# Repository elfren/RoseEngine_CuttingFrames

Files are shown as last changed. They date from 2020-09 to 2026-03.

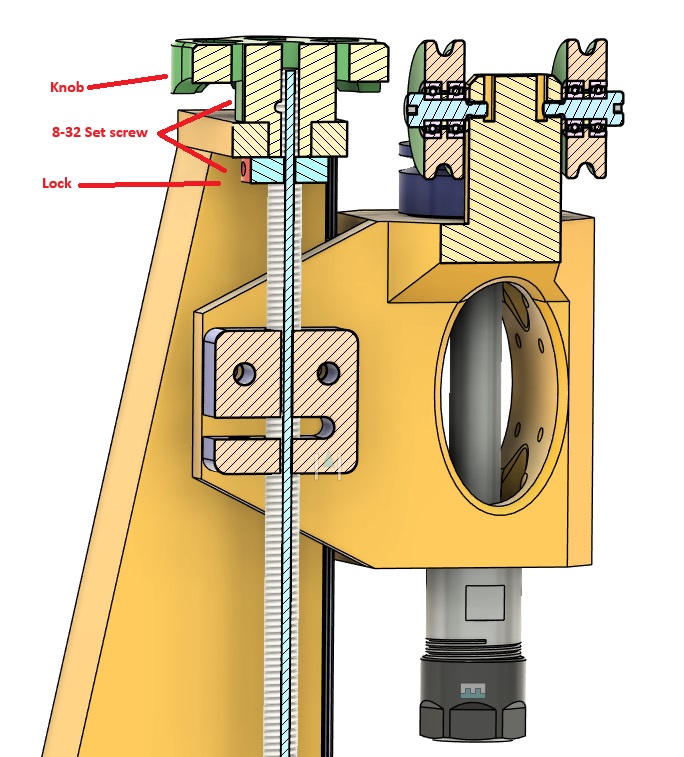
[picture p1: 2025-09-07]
3d_Printed_Frames/VerticalDrillingFrame/LeadscrewAssembly.jpg

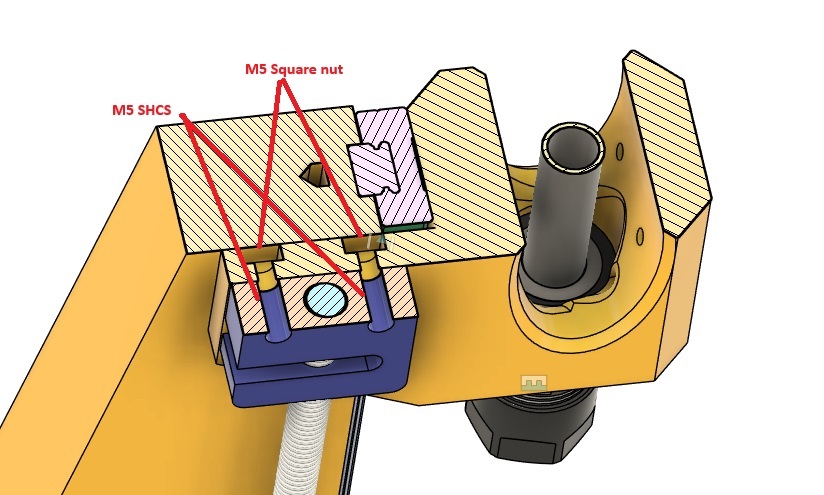
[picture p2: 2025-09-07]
3d_Printed_Frames/VerticalDrillingFrame/LeadscrewNut.jpg

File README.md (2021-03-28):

Fusion 360 models for rose engine cutting frames with adjustable pulley for belt length.

Two models are provided.  
    Sliding: The overhead drive pulley is attached to a slider which moves up and down to adjust belt tension.
    Slotted: The overhead drive pulley slides up and down in a slot.
Part numbers are McMaster-Carr numbers.

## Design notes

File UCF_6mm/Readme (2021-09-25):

UCF which takes 6mm or smaller cutters.

 Toolpaths for the tower are included.  Machining the other parts will probably be on manual machines. 
 The bearing holes should be bored with the arms attached.  
 The holes for the split pins should be drilled after the bearing holes and while the cutter mount arms are still attached to the main arm.

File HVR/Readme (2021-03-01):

Combined horizontal, vertical, and right angle cutting frame.

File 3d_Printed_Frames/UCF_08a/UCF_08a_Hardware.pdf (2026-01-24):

### Main Body Hardware

Qty Description
4 M695ZZ bearing
1 M5x20 shoulder bolt M4x0.7 thread 2 M5x10 shoulder bolt M4x0.7 thread 1 M5x30 shoulder bolt M4x0.7 thread 4 M4x7x7x3 square nut
1 M4x12x12x1 square washer
1 16x150x1.5 Stainless tube
1 M5x12x12x1 square washer 1 5x0.2 bearing shim
6 M3x5.5x2.25 square nut
6 M3x6 set screw
1 Bearing spacer 5mm X 8mm X 5.5mm (Brass tube or printed) 1 2mm X 310mm round poly belt
1 3mm round poly belt (Length depends on overhead drive)

### Insert Cutter Head Hardware

1 TDHB07T1202 Triangular Insert
1 M2.2x6 Torx insert screw
1 Bearing spacer 5mm X 8mm X 6mm (Brass tube or printed) 2 M695ZZ bearing
1 Brass flat stock 4.5mm X 6.5mm X 3mm

### Round Cutter Head Hardware

1 Engraving bit 0.125"
2 M3x6mm set screw
1 Bearing spacer 5mm X 8mm X 6mm (Brass tube or printed) 2 M695ZZ bearing
3 M5x6mm set screw

### Main Body 3D Print (ABS-GF)

1 UCF_08_MainBody + Supports
2 Idler Pulley
1 Double Pulley
1 Bearing spacer 5mm X 8mm X 5.5mm (Brass tube or printed) 1 Knob

### Insert Cutter Head 3D Print (ABS)

1 Cutter Head
1 Bearing spacer 5mm X 8mm X 6mm (Brass tube or printed) 1 Insert Top Lock. This is optional for insert cutter heads.

### Round Cutter Head 3D Print (ABS)

1 Cutter Head
1 Bearing spacer 5mm X 8mm X 6mm (Brass tube or printed) 1 Sharpening jig 60 degrees
1 Sharpening jig 90 degrees
1 Sharpening jig 120 degrees

### Tools

Metric Allen wrench set
M3 Tap (Round engraving bit cutter head) M2.2 Tap (Insert nut cutter head)
1.75mm drill or #51 (0.067") for M2.2 thread .125" drill (Round engraving bit cutter head)

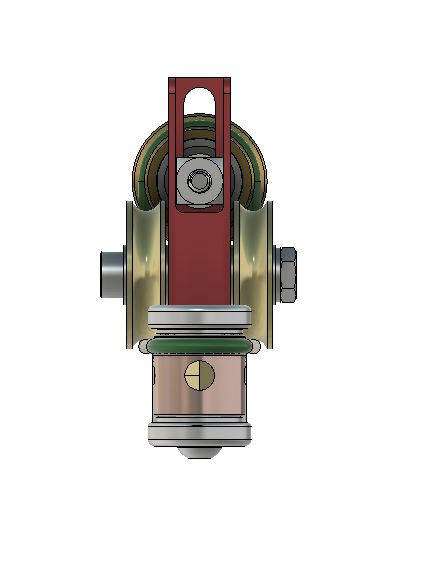
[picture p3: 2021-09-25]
UCF_6mm/Images/UCF_6mm_U_Front.JPG

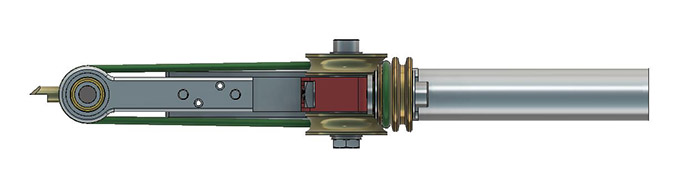
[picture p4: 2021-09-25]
UCF_6mm/Images/UCF_6mm_U_Top.JPG

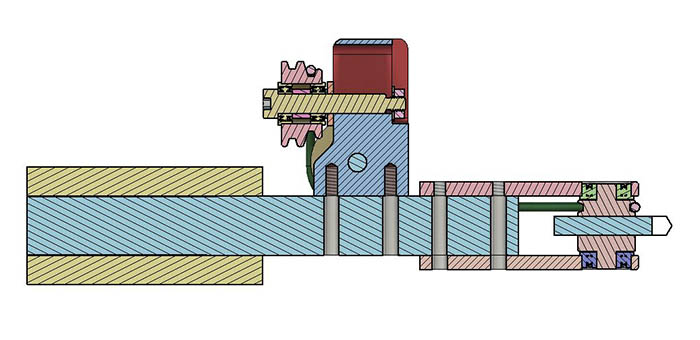
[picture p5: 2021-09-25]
UCF_6mm/Images/SectionView.JPG

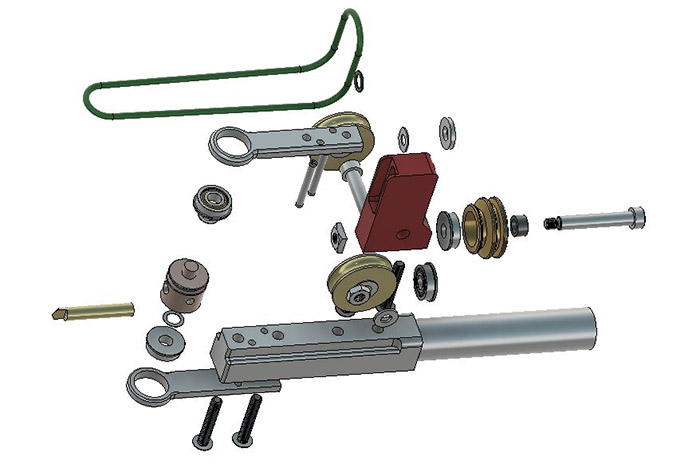
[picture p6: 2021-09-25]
UCF_6mm/Images/UCF_6mm_U_Explode.JPG

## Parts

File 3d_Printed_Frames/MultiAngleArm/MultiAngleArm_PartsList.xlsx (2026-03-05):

Part Name | Quantity | Material | Fasteners
Multi_Angle_Arm | 1 | ABS-GF | M3 Square Nut | 3
Modifier_TF | 1 | ABS-GF | M4 Square Nut | 2
Shaft 0.75"x4" | 1 | Steel | M5 Square Nut | 5
MGN12x100mm Rail | 1 | Steel | M3x6 Set Screw | 4
MGN12C Carriage | 2 | Steel | M5x6 Set Screw | 3
IdlerAdjuster | 1 | ABS-GF | M3x8 SHCS | 4
Leadscrew T8x150mm | 1 | Steel | M3x10 SHCS | 6
TR8x2 AntiBacklash Nut | 1 | Steel | M4x10 SHCS | 2
Leadscrew Lock | 1 | ABS,Brass, or Steel | M5x12 SHCS | 2
HTD-3-60t | 1 | ABS-GF | M4x10 Shoulder Bolt (M3x6mm thread) | 2
Stepper_NEMA17 | 1 | Steel
GT2-3-15t or HTD-3-15t | 1 | Aluminum or ABS-GF
GT2-3 or HTD-3 Timing Belt 80T, 240L,6mm | 1 | Steel
Drilling Frame
DrillFrame_Housing | 1 | ABS-GF | M4 Square Nut | 2
IdlerPulley M695_ZZ | 2 | ABS-GF | M3x6 Set Screw | 2
Spacer_Idler 5x7.5x1.5 | 1 | ABS,Brass, or Steel | M3x8 SHCS | 8
M695 bearing | 2 | Steel | M5x10 Shoulder Bolt | 2
C12-ER16-L100 | 1 | Steel
MR6201_ZZ Bearing | 2 | Steel
Pulley_12mm_Bore | 1 | ABS-GF
C20-ER25-L100 or C20-ER16-100L | 1 | Steel
MF6804_ZZ Bearing | 2 | Steel
Pulley_20mm_Bore | 1 | ABS-GF
UCF
UCF_Base_05c | 1 | ABS-GF | M4_Nut | 2
UCF_Top | 1 | ABS-GF | M4 Square Nut | 2
Idler_Pulley_M695_ZZ | 4 | ABS-GF | M4_Washer | 2
M695_ZZ Bearing | 6 | Steel | M5x6 Set Screw | 8
DoublePulley | 1 | ABS-GF | M5x25 Shoulder Bolt | 3
Spacer_DoublePulley 5x7x4.3 | 1 | ABS,Brass, or Steel | M5x20 Shoulder Bolt | 1
Shaft_10x100 | 1 | Steel
BearingShim_5x7 | 2 | Steel
Round Poly Belt 2x300 | 1 | Polypropylene
Cutter Heads
CutterHead_TDHB071202_CW_Nut | 1 | ABS | M2.2x0.45 Torx Head Screw | 1
Spacer_5x7x6.1 | 1 | ABS,Brass, or Steel
M695_ZZ Bearing | 2 | Steel
TDHB07T1202 | 1 | Carbide
Insert_Top_Lock | 1 | ABS
InsertNut_CW | 1 | Brass
CutterHead_TDHB071202_CCW_Nut | 1 | ABS | M2.2x0.45 Torx Head Screw | 1
Spacer_5x7x6.1 | 1 | ABS,Brass, or Steel
M695_ZZ Bearing | 2 | Steel
TDHB07T1202 | 1 | Carbide
Insert_Top_Lock | 1 | ABS
InsertNut_CCW | 1 | Brass
CutterHead_TDHB071202_CW | 1 | ABS | M2.2x0.45 Torx Head Screw | 1
Spacer_5x7x6.1 | 1 | ABS,Brass, or Steel
M695_ZZ Bearing | 2 | Steel
TDHB07T1202 | 1 | Carbide
Insert_Top_Lock | 1 | ABS
CutterHead_TDHB071202_CCW | 1 | ABS | M2.2x0.45 Torx Head Screw | 1
Spacer_5x7x6.1 | 1 | ABS,Brass, or Steel
M695_ZZ Bearing | 2 | Steel
TDHB07T1202 | 1 | Carbide
Insert_Top_Lock | 1 | ABS
CutterHead_Round | 1 | ABS | M3x6 Set Screw | 2
Spacer_5x7x6.1 | 1 | ABS,Brass, or Steel | M5x6 Set Screw | 3
M695_ZZ Bearing | 2 | Steel
0.125" diameter cutter | 1 | Carbide
Sharpening Jig 60 degree | 1 | ABS
Sharpening Jig 90 degree | 1 | ABS
Sharpening Jig 120 degree | 1 | ABS

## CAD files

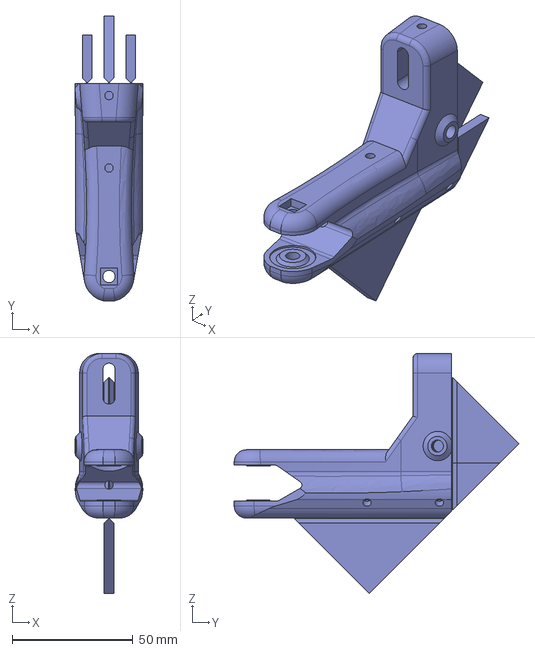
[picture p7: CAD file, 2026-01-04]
3d_Printed_Frames/UCF_08a/MainBody/UCF_08_MainBody/MainBody_3D_UCF_Insert_08_WithSupports.step
28.2 x 117.9 x 99.5 mm

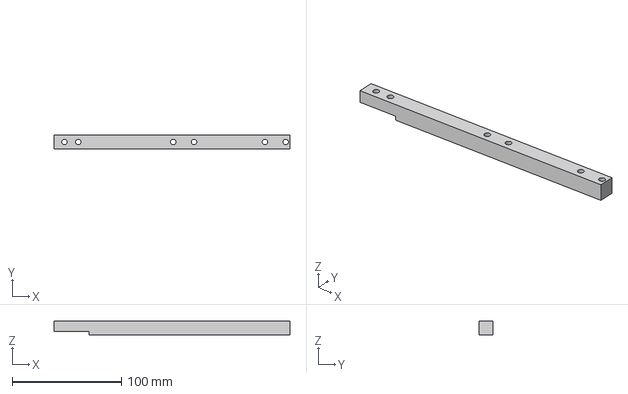
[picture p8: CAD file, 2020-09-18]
Horizontal/Models/Step/MainArm_Square.step
215.9 x 12.7 x 12.7 mm

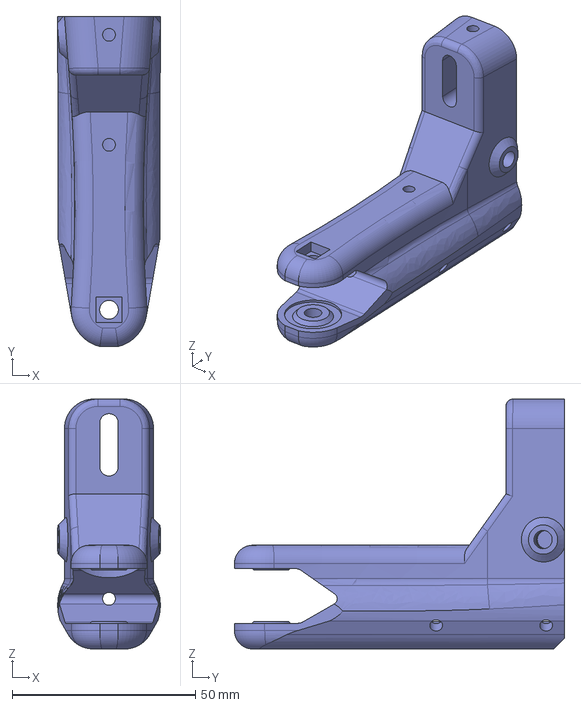
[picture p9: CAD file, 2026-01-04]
3d_Printed_Frames/UCF_08a/MainBody/UCF_08_MainBody/MainBody_3D_UCF_Insert_08.step
28.2 x 90.1 x 68.2 mm

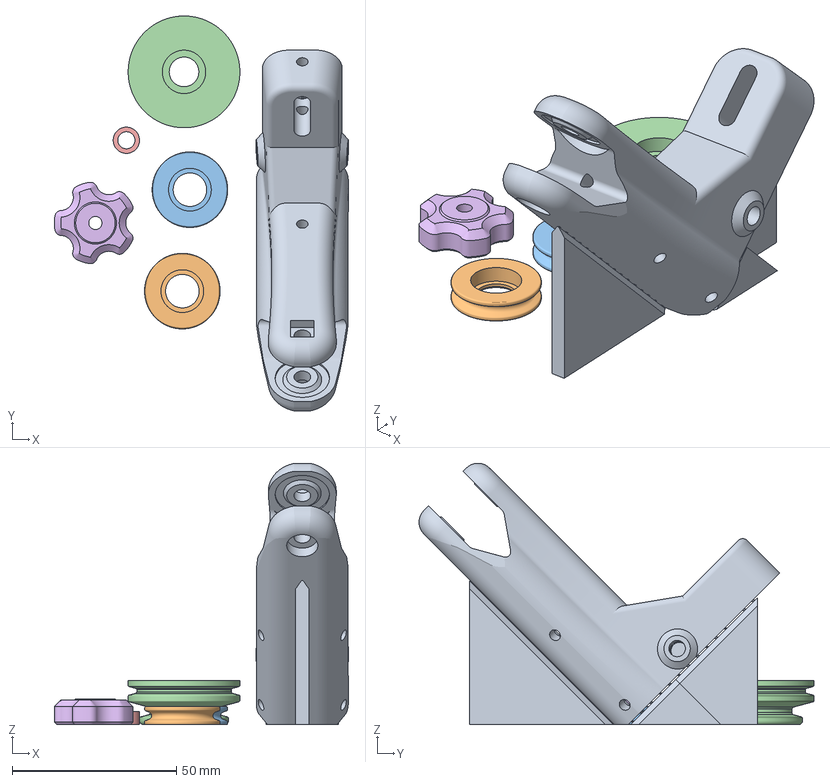
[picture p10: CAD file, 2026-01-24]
3d_Printed_Frames/UCF_08a/UCF_08a_Main.3mf
89.6 x 120.2 x 79.6 mm
MainBody_3D_UCF_Insert_08_WithSupports.step
Idler_5mm.step x 2
DoublePulley_08_UCF.step
Spacer_DoublePulley_08UCF.step
Knob_03.step

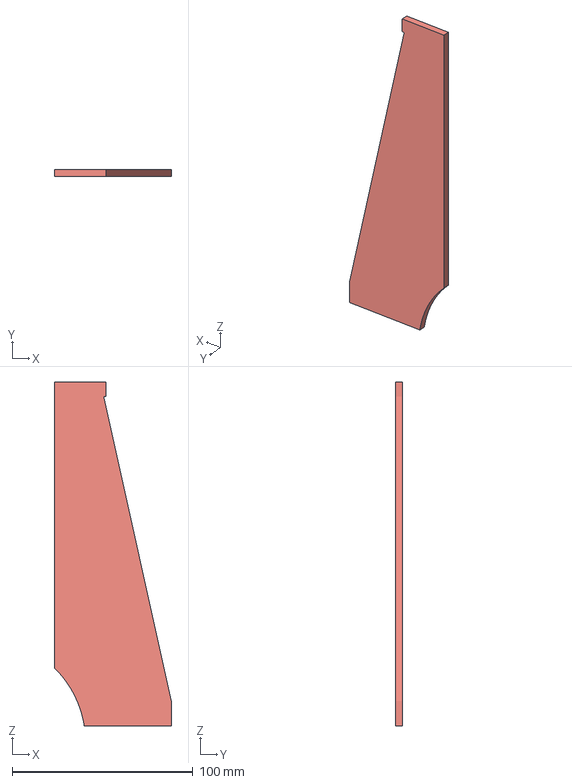
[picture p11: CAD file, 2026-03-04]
3d_Printed_Frames/MultiAngleArm/3DPrint_Slicer_Files/MAA_Modifier_MainArm.3mf
64.8 x 4.00 x 190.1 mm

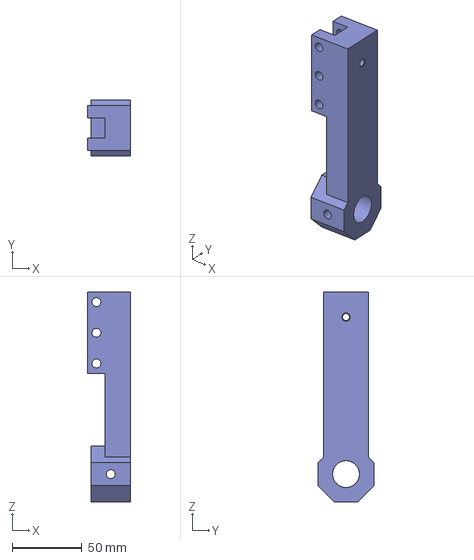
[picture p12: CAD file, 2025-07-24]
3d_Printed_Frames/Angle/MainArm_04.step
30.5 x 40.0 x 150.6 mm

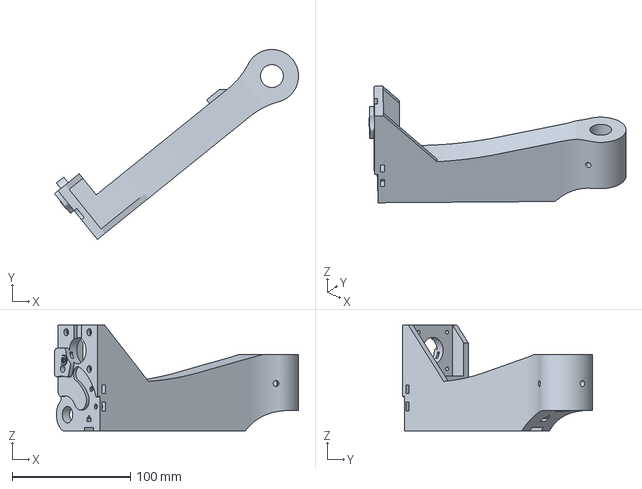
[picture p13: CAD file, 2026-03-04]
3d_Printed_Frames/MultiAngleArm/3DPrint_Slicer_Files/MAA_MainArm.3mf
206.6 x 160.8 x 89.4 mm

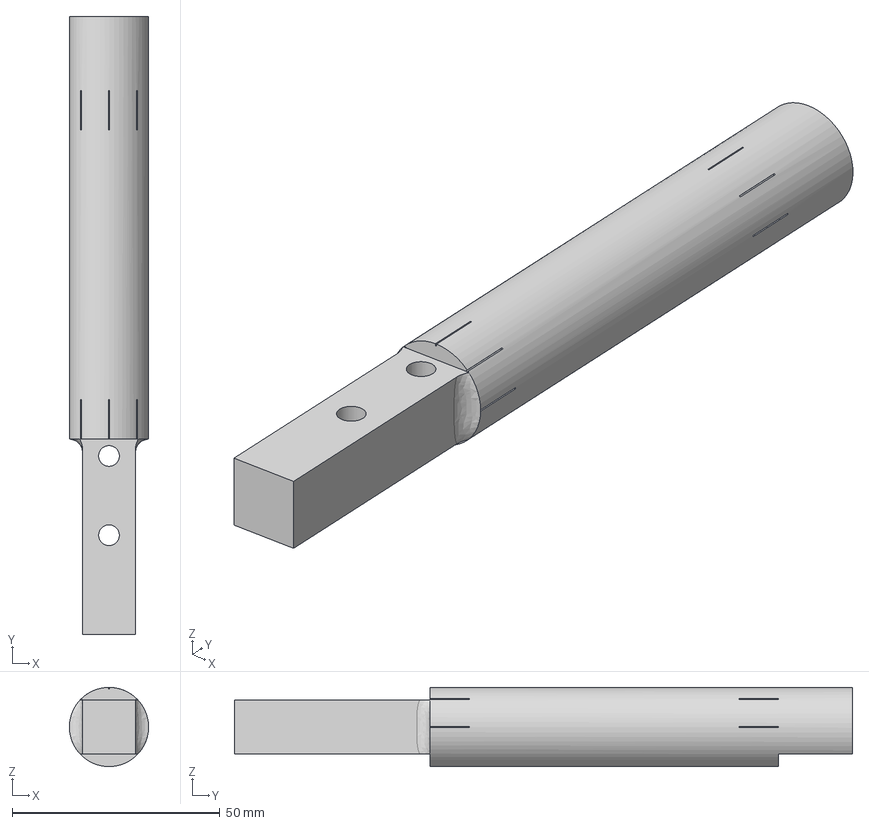
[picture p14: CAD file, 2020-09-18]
UCF-Slotted/Models/Step/UCF_MainArm.step
19.0 x 148.6 x 19.0 mm

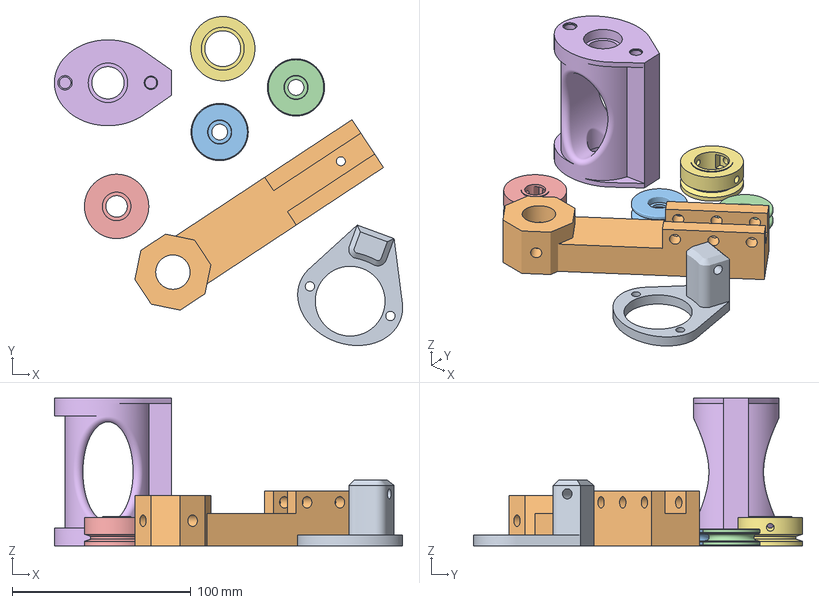
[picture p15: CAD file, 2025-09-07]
3d_Printed_Frames/Angle/AngleDrillFrame_12_and_20mm_Bore.3mf
194.8 x 184.0 x 82.5 mm
PulleyStand_04.step
MainArm_04.step
IdlerPulley_03.step x 2
Pulley_12mm_Bore.step
Housing_22mm_OD.step
Pulley_20mm_Bore.step

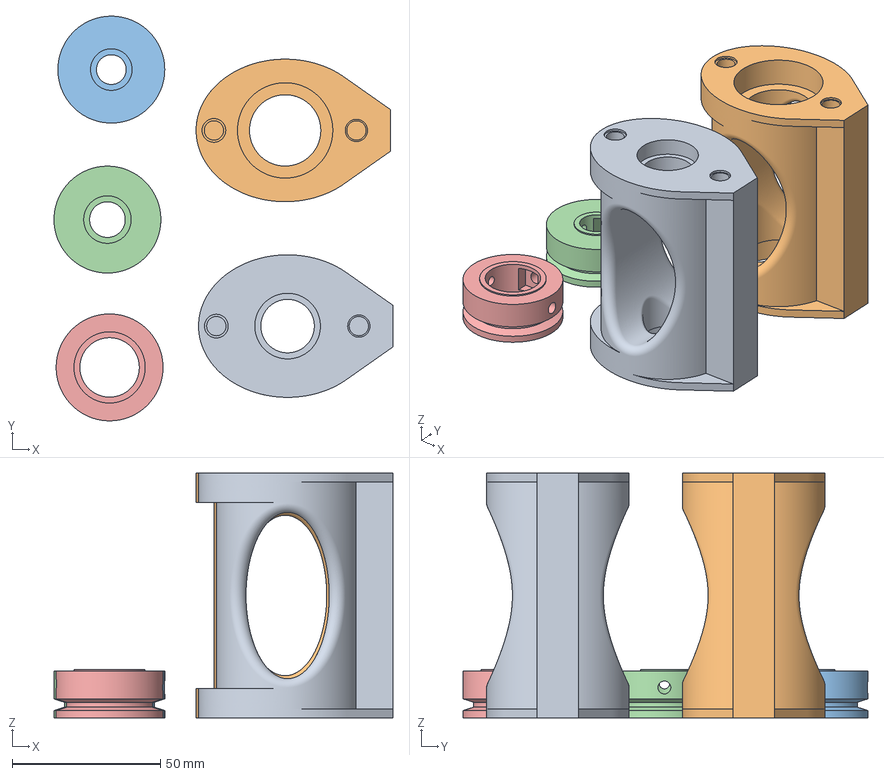
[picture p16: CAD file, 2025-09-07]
3d_Printed_Frames/Drilling_Frame/3D_DrillFrame.3mf
114.2 x 136.3 x 82.5 mm
Housing_22mm_OD.step
Housing_32_OD.step
Pulley_10mm_Bore.step
Pulley_12mm_Bore.step
Pulley_20mm_Bore.step

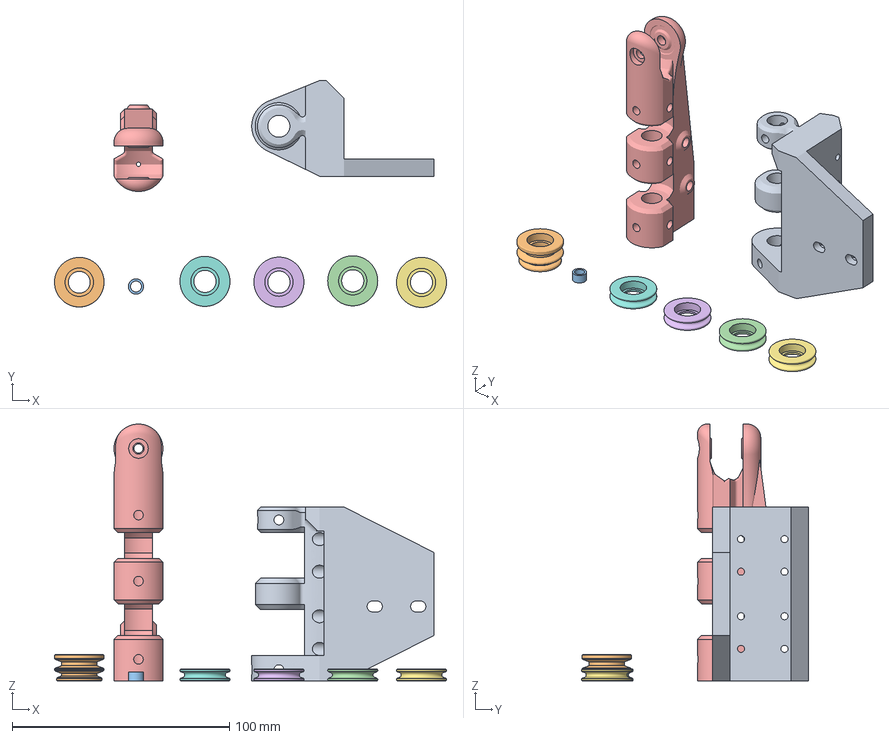
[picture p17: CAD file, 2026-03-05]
3d_Printed_Frames/MultiAngleArm/3DPrint_Slicer_Files/MAA_UCF .3mf
180.3 x 104.3 x 118.2 mm
Base_05c .step
DoublePulley_08.step
DoublePulley_Spacer.step
Idler_5mm.step x 4
MAA_UCF.step

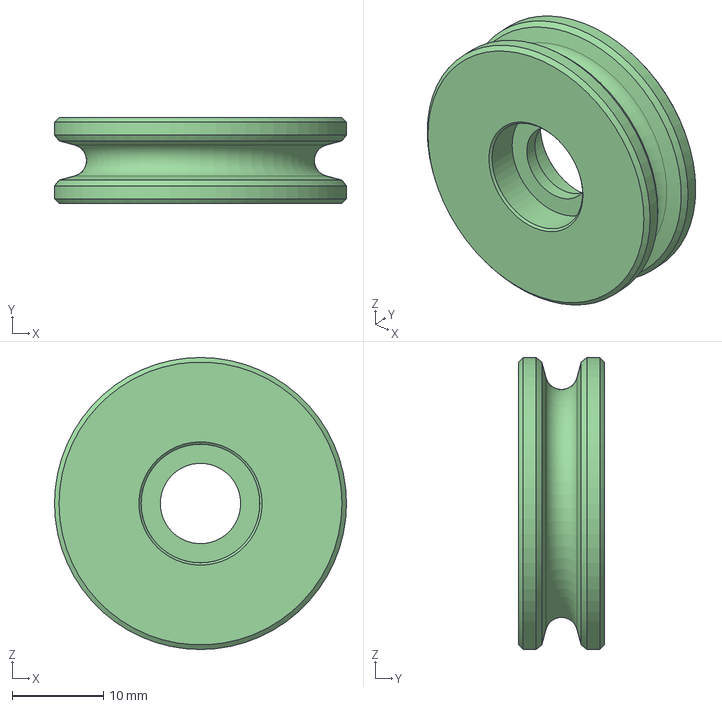
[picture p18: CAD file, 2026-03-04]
3d_Printed_Frames/MultiAngleArm/Drill_Frame/IdlerPulley_03.step
32.0 x 9.40 x 32.0 mm

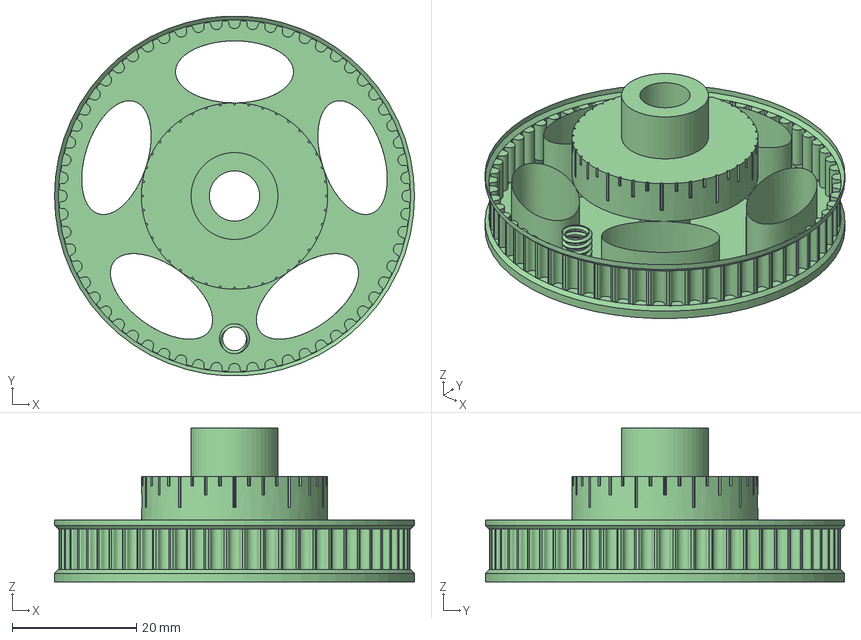
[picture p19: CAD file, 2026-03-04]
3d_Printed_Frames/MultiAngleArm/Main_Arm/Pulley_HTD-3-60t.step
58.0 x 57.9 x 24.8 mm

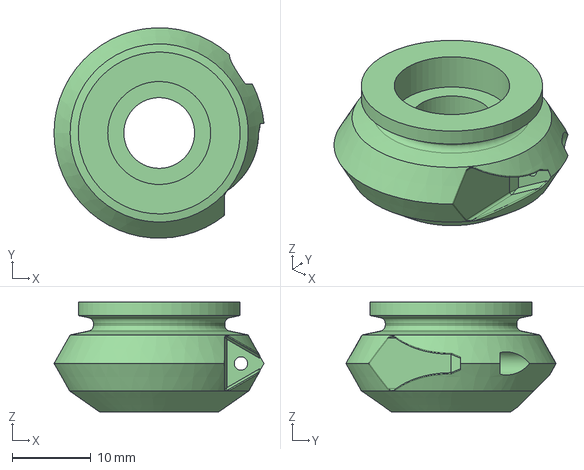
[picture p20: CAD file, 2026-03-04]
3d_Printed_Frames/MultiAngleArm/UCF/Insert_CutterHead/Plain/CutterHead_TDHB071202_CW.step
26.7 x 26.8 x 14.0 mm

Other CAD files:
3d_Printed_Frames/MultiAngleArm/UCF/MAA_UCF.step
3d_Printed_Frames/MultiAngleArm/UCF/Round_CutterHead/Cutterhead_Round_10b.step
3d_Printed_Frames/MultiAngleArm/UCF/Round_CutterHead/SharpeningJigs/Jig_60.step
3d_Printed_Frames/UCF_08a/CutterHeads_HexNuts/CutterHead_TPGH080201_CCW.gcode.3mf
3d_Printed_Frames/Angle/AngleDrillFrame_10mm_Bore.3mf
3d_Printed_Frames/Angle/IdlerPulley v7.step
3d_Printed_Frames/Angle/IdlerPulley_03.step
3d_Printed_Frames/Angle/InfillModifier_04.3mf
3d_Printed_Frames/Angle/PulleyStand_04.step
3d_Printed_Frames/Archive/3D_UCF.3mf
3d_Printed_Frames/Archive/3D_UCF.f3z
3d_Printed_Frames/Archive/3D_UCF_B_CutterHead_104zz.step
3d_Printed_Frames/Archive/3D_UCF_B_DoublePulley.step
3d_Printed_Frames/Archive/3D_UCF_B_Idler.step
3d_Printed_Frames/Archive/3D_UCF_Cutterheads.3mf
3d_Printed_Frames/Archive/CutterJig_120Degrees.step
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

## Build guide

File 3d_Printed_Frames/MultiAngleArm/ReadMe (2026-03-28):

Step files for each part are located in their individual folders. .3mf files are located in the folder, 3DPrint_Slicer_Files, as well as the individual folders.

Cutter heads are shared with UCF_08a.

Multi Angle Main Arm print files and filament type:
  MAA_MainArm.3mf (ABS-GF)
  MAA_Modifier_MainArm.3mf (Loaded as modifier in MAA_MainArm.3mf. 100% infill)
  MAA_Pulleys.3mf (ABS)
  
Drilling Frame:
  DrillFrame.3mf (ABS-GF)

UCF:
  MAA_UCF.3mf (ABS-GF)
  CutterHeads_Nuts.3mf (ABS)
  CutterHead_Round.3mf (ABS)

Notes:
Main arm should be printed on a raft to reduce warping.

Cutter heads should be printed with a 0.08mm layer height.  The others may be printed with a 0.2mm layer height (0.08mm layer height is OK, but will take much longer to print).
Insert cutter heads have CW and CCW versions. The round cutter head uses 0.125" engraving bits and can be configured for either CW or CCW.

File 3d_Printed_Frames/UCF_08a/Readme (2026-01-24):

Full assembly instructions are located in '3D Printed Universal Cutting Frame 8a.pdf'.
.3mf files include print profiles.
Step files are included in order to make modifications easier.

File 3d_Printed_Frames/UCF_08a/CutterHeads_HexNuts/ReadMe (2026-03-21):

These cutter heads use TDHB07T1202-PCD and TPGH080201-PCD diamond inserts. Each have CW and CCW versions.

The TPGH insert has an 11 degree top rake. The TDHB does not have a top rake.

The TDHB uses an M2.2x0.45 or a #2-56 torx head insert screw. A #2-56 nut is used. When using the M2.2 screw, tapping the nut with an M2.2 tap will ensure the threads won't bind.
 
The TPGH uses M2.5x0.45 torx head insert screw and M2.5 nuts. 

The TopLock is secured with ABS slurry (Acetone and ABS).  It provides more support for the insert.

Print these with ABS. Gcode files are sliced for a Bambu X1C with a 0.4mm nozzle. Layer height is .08mm.

The image shows the TPGH cutter head with supports for printing.

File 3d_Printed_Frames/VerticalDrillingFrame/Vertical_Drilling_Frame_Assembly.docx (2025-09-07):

# Vertical Drilling Frame Assembly

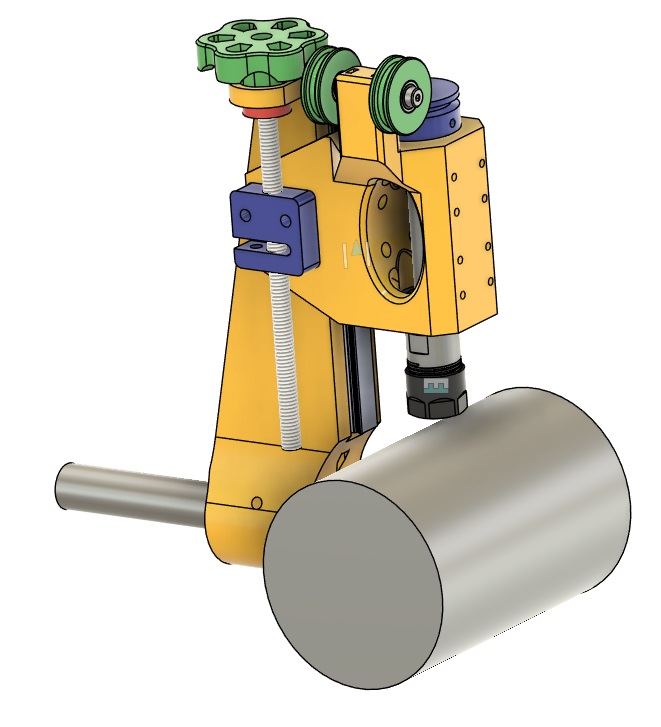
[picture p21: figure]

# Parts List:

ER Chuck Housing
QTY | Hardware
1 | MGN12 rail. 150mm long
2 | MGNC carriage
4 | M3x8mm SHCS
2 | M3x12mm SHCS
1 | C12-ER16-100L
2 | M5x10mm Shoulder Bolt with M4 threads (6mm long)
2 | M5x0.2 Bearing Shim
2 | M5 Washer 1mm thick
2 | M4 Square Nut
2 | 8-32x0.1875" Set Screw
2 | M5 Square Nut
2 | MR6201_ZZ Bearing
4 | MR695_ZZ Bearing
Main Arm
3 | M5x5mm Set Screw
3 | M5 Square Nut
1 | 0.75"x5" Steel Shaft
1 | 250-104 Boring Bar Tool Holder
2 | M3 Square Nut

Leadscrew
1 | TR8 Leadscrew 2mm pitch, 2mm lead
1 | Anti-Backlash Nut to fit
2 | M5x20 SHCS
5 | 8-32x0.1875" Set Screw
| 3D printed parts
1 | ER Chuck Housing
2 | Idler Pulley
2 | Idler Spacer (5x7x1.5mm)
1 | Drive Pulley
1 | Leadscrew Knob
1 | Leadscrew Lock
1 | Main Arm

# Main Arm:

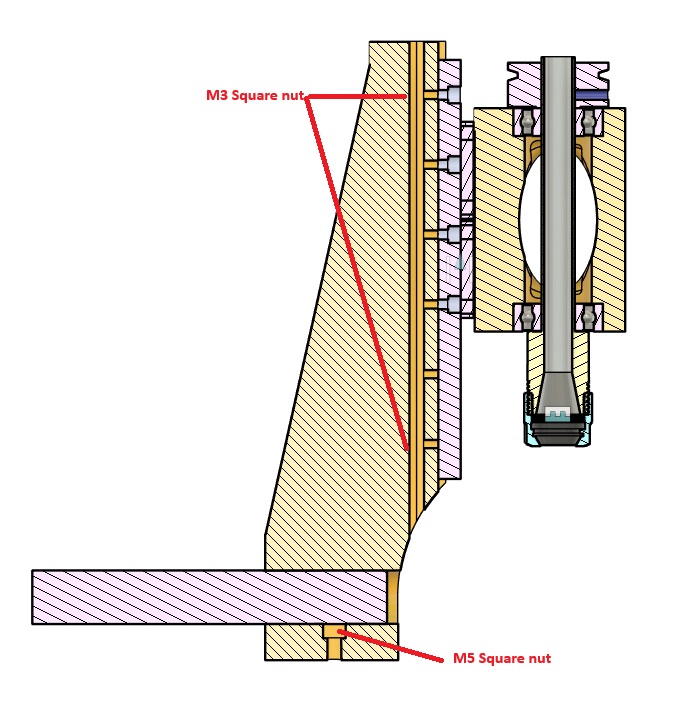
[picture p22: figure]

M3 tap 6 of the 8 holes to attach linear slide to arm. Drill the two end holes with 1/8th inch or 3.5mm drill. Insert the two M3 square nuts. Note: M3 nuts can be used on all of the holes, but may be difficult to install.

Attach the ¾” shaft to the arm using the M5 square nuts and set screws. Note: M5 SHCS may be used instead of the set screws.

Attach the linear rail to the arm.

# Spindle Housing:

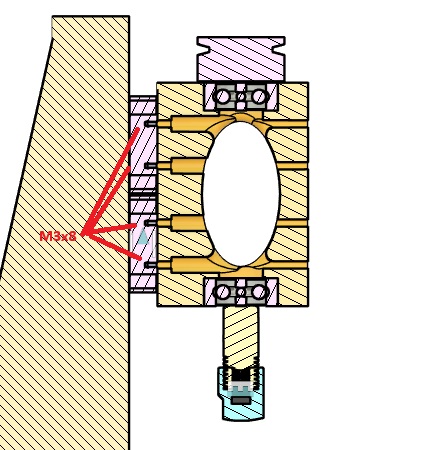
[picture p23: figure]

Press the MR6201_ZZ bearings into the housing.

Fasten the housing to the linear rail carriages using M3x8 SHCS.

Install the ER16 chuck.

Install the drive pulley using two 8-32 set screws.

# Idler Pulleys:

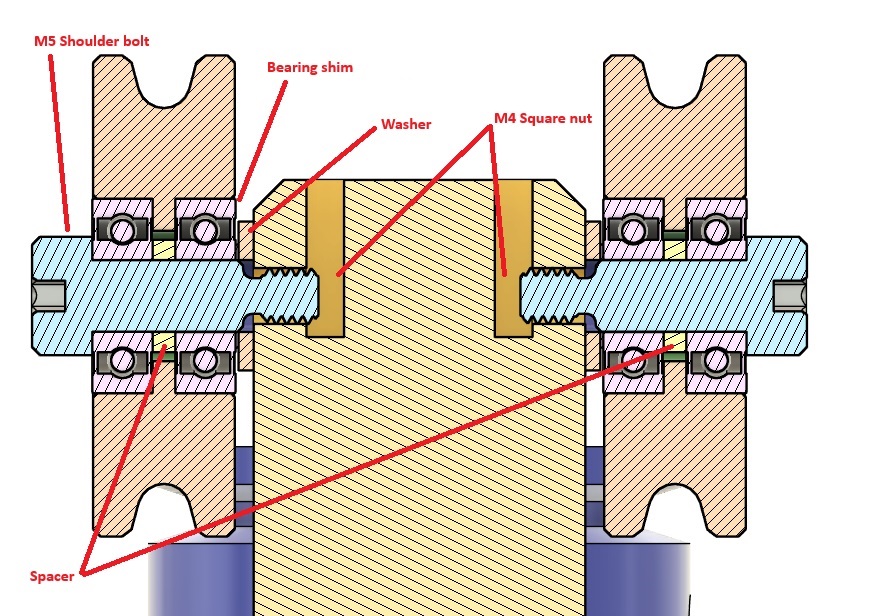
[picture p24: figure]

Press the M4 square nuts into the top of the housing.

Press the MR695_ZZ bearings into the idler pulleys making sure the spacer is installed. Insert the M5 shoulder bolt, add the bearing shim and the washer, then attach the idler pulley to the housing.

# Leadscrew


Install M5 square nuts in the housing. Attach the anti-backlash nut using M5 screws.


Tap the knob and the lock for 8-32 set screws.

Attach the knob, lock, and leadscrew.

# 3D Print

VerticalDrillFrame.3mf is optimized for a Bambu X1C printer.

Print Settings:

- 8 Walls
- 40% Infill, Cubic pattern
- Main Arm has a 100% infill modifier in the center
- Support: Tree Slim

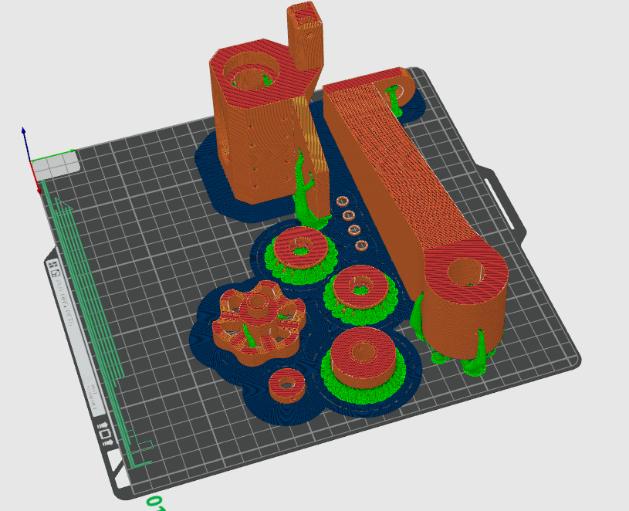
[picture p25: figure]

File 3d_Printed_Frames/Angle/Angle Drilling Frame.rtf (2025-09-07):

Angle Drilling Frame

This uses the 3d printed drilling frame in addition to a rotatable arm. It is held in an AXA boring bar holder.
Parts List:
Quantity | Description
4 | 695 Bearing (no flange) used in the idler wheels
2 | M5x10 Shoulder bolt with M4 thread
8 | M5 Heat set insert
2 | M4 Heat set insert
1 | 3/4"x4.125" Steel rod
6 | M5x12 SHCS
1 | AXA holder 250-104
1 | 3d printed drill frame with ER chuck
2 | 3d printed pulleys
1 | 3d printed main arm
1 | 3d printed pulley mount

3d Print Settings:
Setting | Value
Filament | ABS-GF
Walls | 8
Infill % | 40
Infill Pattern | Cubic
Support | Tree Slim
Brim | Outer 15mm

The file, AngleDrillFrame_10mm_Bore.3mf, contains all of the parts for the drill frame housing and the angle drill frame parts for an ER chuck with a 10mm shaft.
The file, AngleDrillFrame_12_and_20mm_Bore.3mf, contains all of the parts for the drill frame housing and the angle drill frame parts for an ER chuck with a 20mm and a 12mm shaft (Only the pulley differs).

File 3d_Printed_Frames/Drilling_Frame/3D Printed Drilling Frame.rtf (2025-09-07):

3D Printed Drilling Frame

There are two 3d printed parts, the main housing (green), and the drive pulley (yellow). The housing is designed to fit in an AXA tool holder. There are two versions of the main housing, one using 32mm OD bearings, and one using 22mm OD bearings. There are three versions of the pulley, one for each shank diameter; 20mm, 12mm, and 10mm. Any ER chuck with one of those shank diameters will work. The chuck must be at least 100mm long. 150mm chucks will also work. 20mm shanks will use F6804ZZ or 6804ZZ bearings. 12mm shanks will use F6201ZZ or 6201ZZ bearings. 10mm shanks will use F6900ZZ or 6900ZZ bearings.
The pulley is secured with two 8-32 x ¼” set screw in captured 8-32 square nut
Parts List

Quantity | Description
1 | 3d printed housing
1 | 3d printed Pulley
1 | ER Chuck
2 | 8-32 square nut
2 | 8-32 x 1/4" set screw
2 | Bearings

3d Print Settings:
Setting | Value
Filament | ABS-GF
Walls | 8
Infill % | 40
Infill Pattern | Cubic
Support | Tree Slim
Brim | Outer 15mm

The file, 3D_DrillFrame.3mf, contains all of the versions. Remove the unwanted ones before printing.

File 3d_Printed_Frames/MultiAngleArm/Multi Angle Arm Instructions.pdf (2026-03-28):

# Multi Angle Arm

## With

# Drilling Frame and Universal Cutting Frame

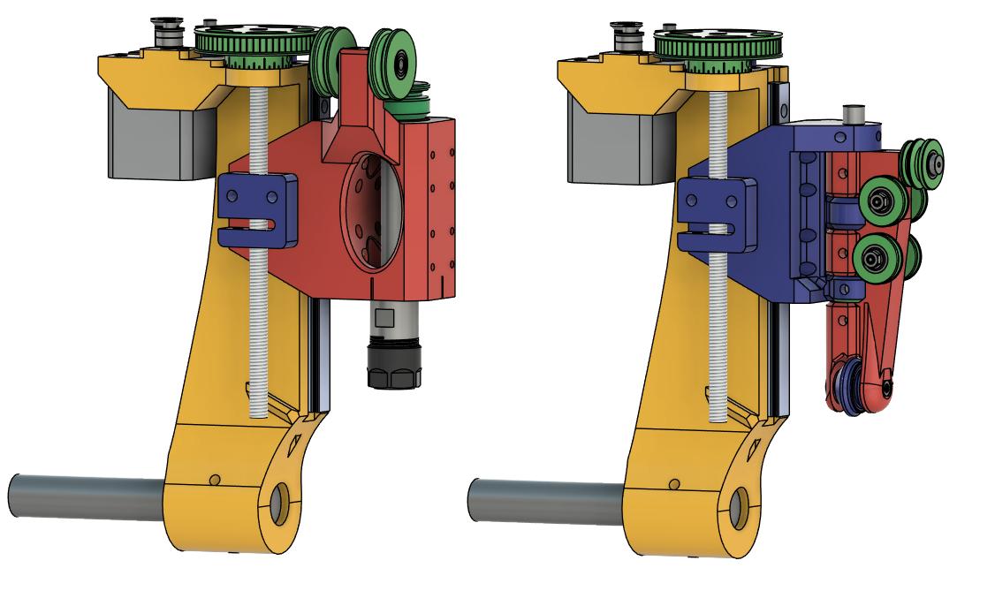
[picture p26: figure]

### The MultiAngleArm (MAA) is designed to hold a cutter above the workpiece at any angle between 90 and 180 degrees. The drilling frame rotates the tool parallel to the arm while

the universal cutting frame rotates the tool perpendicular to the arm and can be positioned

### at an angle to the arm. The stepper motor allows the depth of cut to be set

programmatically as well as moving the cutter in and out of the workpiece at the beginning and end of a cut. The MAA is attached to the toolpost with an AXA boring bar holder.

## Parts List

Part Name | Quantity | Material
Main Arm
Multi_Angle_Arm | 1 ABS-GF
Modifier_TF | 1 ABS-GF
Shaft 0.75"x4" | 1
MGN12x100mm Rail | 1

MGN12C Carriage | 2
IdlerAdjuster | 1 ABS-GF
F604ZZ Bearing | 2
M604ZZ Bearing | 2
Leadscrew T8x150mm | 1
TR8x2 AntiBacklash Nut | 1
Leadscrew Lock | 1 ABS,Brass, or Steel
HTD-3-60t | 1 ABS-GF
Stepper_NEMA17 | 1
GT2-3-15t or HTD-3-15t | 1 Aluminum or ABS-GF
GT2-3 or HTD-3 Timing Belt 80T, 240L,6mm | 1
M3 Square Nut | 3
M4 Square Nut | 2
M5 Square Nut | 5
M3x6 Set Screw | 4
M5x6 Set Screw | 3
M3x8 SHCS | 4
M3x10 SHCS | 6
M4x10 SHCS | 2
M5x12 SHCS | 2
M4x10 Shoulder Bolt (M3x6mm thread) | 2

Drilling Frame
DrillFrame_Housing | 1 ABS-GF
IdlerPulley M695ZZ | 2 ABS-GF
Spacer_Idler 5x7.5x1.5 | 1 ABS,Brass, or Steel
M695 bearing | 2
M4 Square Nut | 2
M3x6 Set Screw | 2
M3x8 SHCS | 8
M5x10 Shoulder Bolt | 2
C12-ER16-L100 | 1
MR6201ZZ Bearing | 2
Pulley_12mm_Bore | 1 | ABS-GF
C20-ER25-L100 or C20-ER16-100L | 1
MF6804ZZ Bearing | 2
Pulley_20mm_Bore | 1 | ABS-GF

UCF
UCF_Base_05c | 1 ABS-GF

UCF_Top | 1 ABS-GF
Idler_Pulley_M695ZZ | 4 ABS-GF
M695ZZ Bearing | 6
DoublePulley | 1 ABS-GF
Spacer_DoublePulley 5x7x4.3 | 1 ABS,Brass, or Steel
Shaft_10x100 | 1
BearingShim_5x7 | 2
Round Poly Belt 2x300 | 1 Polypropylene
M4_Nut | 2
M4 Square Nut | 2
M4_Washer | 2
M5x6 Set Screw | 8
M5x25 Shoulder Bolt | 3
M5x20 Shoulder Bolt | 1

Cutter Heads
CutterHead_TDHB071202_CW_Nut | 1 ABS
Spacer_5x7x6.1 | 1 ABS,Brass, or Steel
M695ZZ Bearing | 2
TDHB07T1202 | 1 Carbide
Insert_Top_Lock | 1 ABS
M2.2x0.45 Torx Head Screw | 1
#2-56 Nut | 1 Brass

CutterHead_TDHB071202_CCW_Nut | 1 ABS
Spacer_5x7x6.1 | 1 ABS,Brass, or Steel
M695ZZ Bearing | 2
TDHB07T1202 | 1 Carbide
Insert_Top_Lock | 1 ABS
M2.2x0.45 Torx Head Screw | 1
#2-56 Nut | 1 Brass

CutterHead_Round | 1 ABS
Spacer_5x7x6.1 | 1 ABS,Brass, or Steel
M695ZZ Bearing | 2
0.125" diameter cutter | 1 Carbide
M3x6 Set Screw | 2
Sharpening Jig 60 degree | 1 ABS
Sharpening Jig 90 degree | 1 ABS
Sharpening Jig 120 degree | 1 ABS

M5x6 Set Screw | 3

Tools
M2.2x0.45 Tap (UCF only)
M1.75 Drill (UCF only)
M3x0.5 Tap
M2.5 Drill
0.125" Drill (UCF only)
Metric Allen Wrenches

## Notes:

When there are multiple options, the preferred option is highlighted in light green and the others in light orange.
Shoulder bolt threads should be 5 to 6mm long.

## Main Arm Assembly

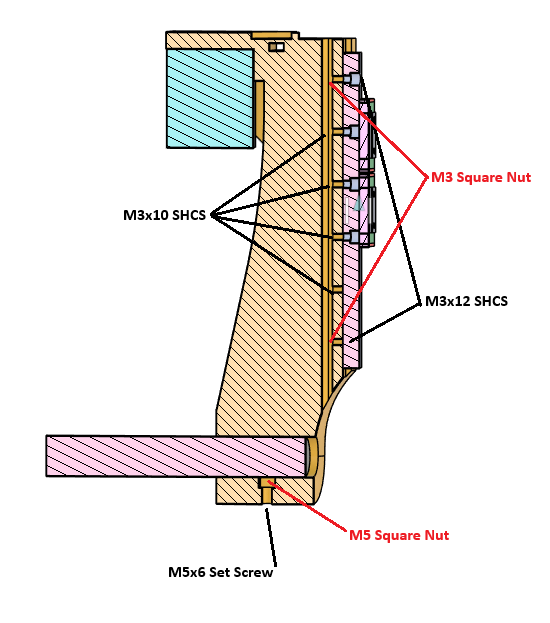
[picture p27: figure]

### Tap the center 4 holes for M3x0.5. Insert M3 square nuts for the two end screws. When

installing the MGN12 rail, leave the rubber bumpers in the end holes until the drilling frame or UCF is installed to prevent the carriages from coming off the rail.
Insert the three M5 square nuts and M5 set screws to lock the shaft.

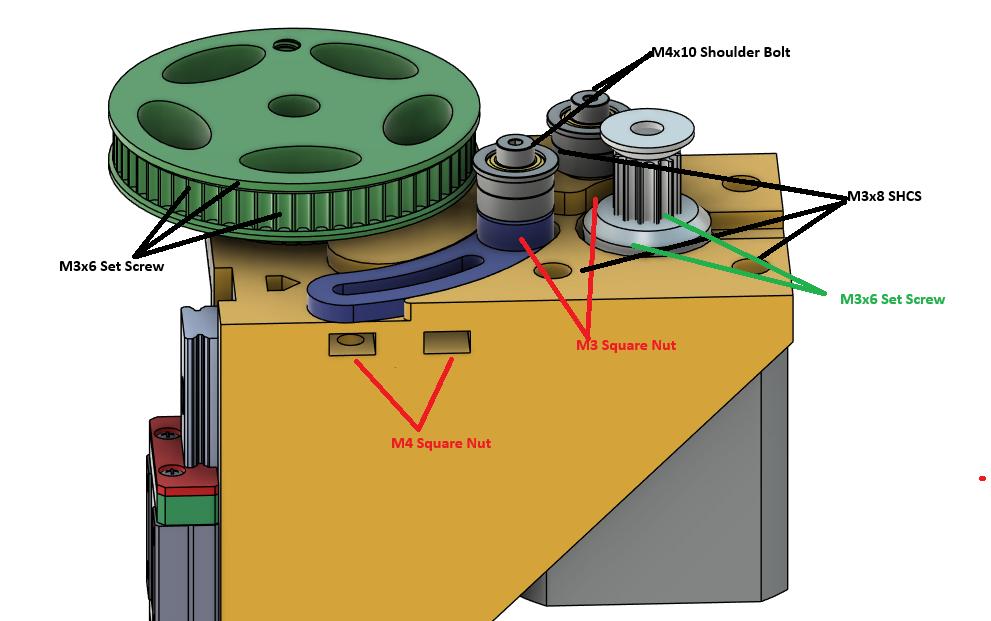
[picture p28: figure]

Attach M604_ZZ and F604_ZZ bearings using M4x10 shoulder bolts and M3 square nuts. Attach adjustable idler using two M4x10 SHCS and M4 washers.
Attach stepper motor using M3x8 SHCS.
Attach Pulley using three M3x6 set screws.

## Drilling Frame

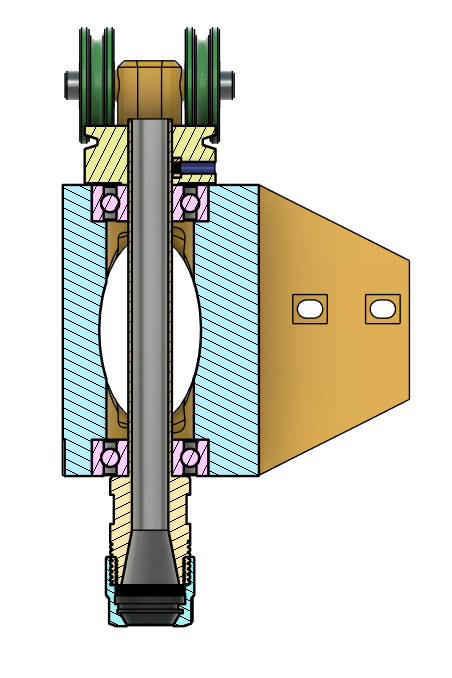
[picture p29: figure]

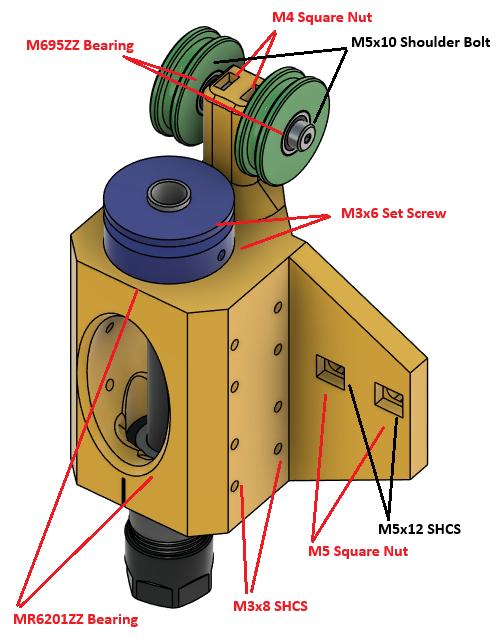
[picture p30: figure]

Tap the double pulley with M3 tap.

## UCF

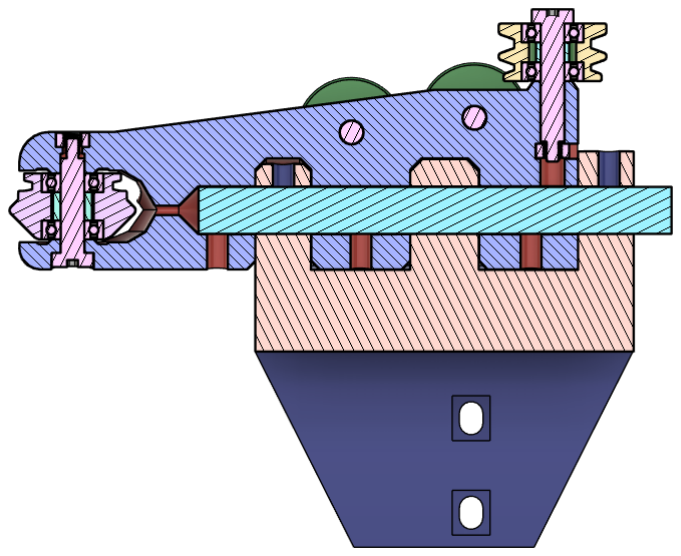
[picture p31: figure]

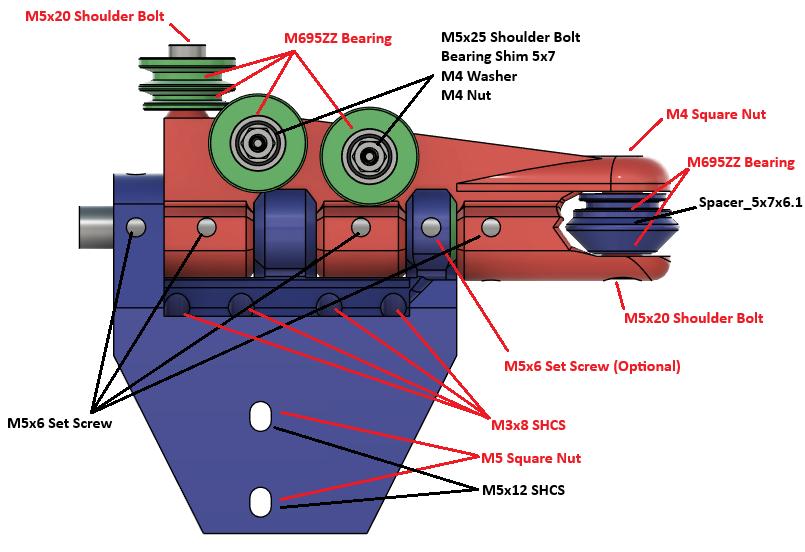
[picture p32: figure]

## Cutter Heads

## Insert Cutter Head

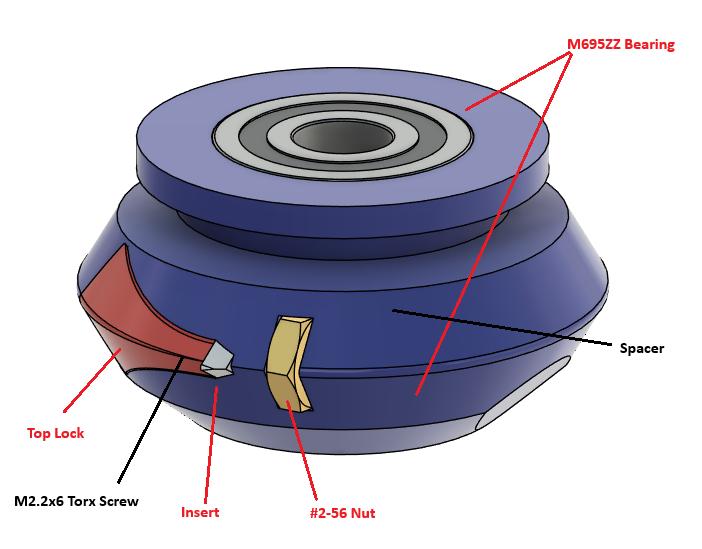
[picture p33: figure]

Use ABS slurry (ABS and Acetone) to secure Top Lock and nut.

## Round Cutter Head

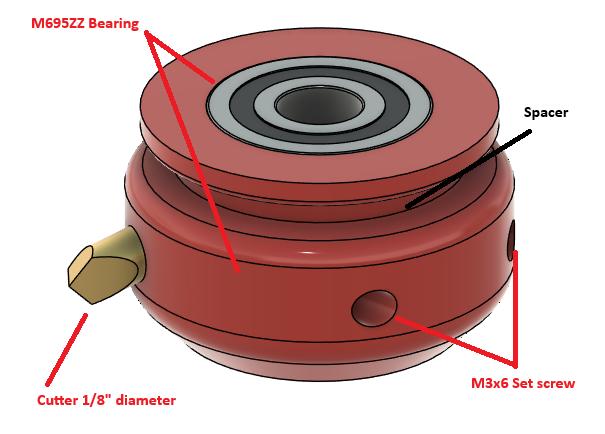
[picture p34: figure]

Tap the holes for the M3 set screws. Depending on how well your printer is calibrated, you may need to drill or ream the hole for the cutter.

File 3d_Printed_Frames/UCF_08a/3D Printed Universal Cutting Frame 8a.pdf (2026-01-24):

## 3D Printed Universal Cutting Frame

## Version 8a

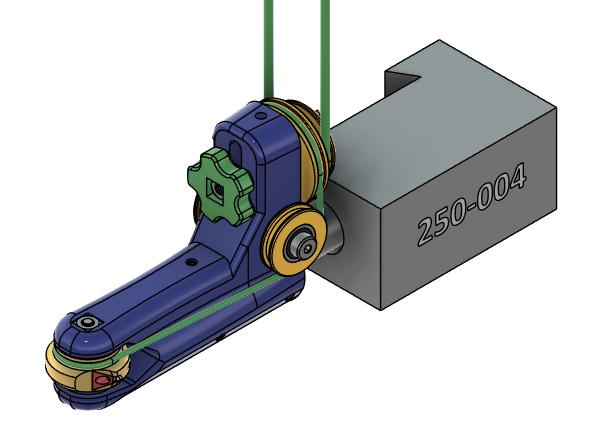
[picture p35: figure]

This cutting frame is used on ornamental lathes and rose engines. It is called universal because it can be rotated plus or minus up to 90 degrees from horizontal in the tool holder. Typical all metal universal cutting frames cost between four and six hundred dollars. Using off the shelf hardware and a 3D printer, this can be made for a fraction of that. An overhead drive with 3mm round poly belting is used to drive the cutter. There are several cutter head options for turning CW and CCW with either triangular carbide inserts or round 1/8” carbide engraving bits. Maximum depth of cut with the triangular inserts is 0.050”, but lighter cuts up to 0.020” are recommended. The round engraving bits have a larger maximum depth of cut, but it is still recommended to use lighter cuts.

## Main Body

## Parts List

Main Body Hardware
Qty Description
4 M695ZZ bearing
1 M5x20 shoulder bolt M4x0.7 thread 2 M5x10 shoulder bolt M4x0.7 thread 1 M5x30 shoulder bolt M4x0.7 thread 4 M4x7x7x3 square nut
1 M4x12x12x1 square washer
1 16x150x1.5 Stainless tube
1 M5x12x12x1 square washer 1 5x0.2 bearing shim
6 M3x5.5x2.25 square nut
6 M3x6 set screw
1 Bearing spacer 5mm X 8mm X 5.5mm (Brass tube or printed) 1 2mm X 310mm round poly belt
1 3mm round poly belt (Length depends on overhead drive)

Insert Cutter Head Hardware
1 TDHB07T1202 Triangular Insert
1 M2.2x6 Torx insert screw
1 Bearing spacer 5mm X 8mm X 6mm (Brass tube or printed) 2 M695ZZ bearing
1 Brass flat stock 4.5mm X 6.5mm X 3mm

Round Cutter Head Hardware
1 Engraving bit 0.125"
2 M3x6mm set screw
1 Bearing spacer 5mm X 8mm X 6mm * 2 M695ZZ bearing
3 M5x6mm set screw

## 3D Print List

Main Body 3D Print (ABS-GF)
1 UCF_08_MainBody + Supports 2 Idler Pulley

1 Double Pulley
1 Bearing spacer 5mm X 8mm X 5.5mm (Brass tube or printed) 1 Knob

Insert Cutter Head 3D Print (ABS)
1 Cutter Head
1 Bearing spacer 5mm X 8mm X 6mm (Brass tube or printed) 1 Insert Top Lock. This is optional for insert cutter heads.

Round Cutter Head 3D Print (ABS)
1 Cutter Head
1 Bearing spacer 5mm X 8mm X 6mm * 1 Sharpening jig 60 degrees
1 Sharpening jig 90 degrees
1 Sharpening jig 120 degrees

Tools
Metric Allen wrench set
M3 Tap (Round engraving bit cutter head) M2.2 Tap (Insert nut cutter head)
1.75mm drill or #51 (0.067") for M2.2 thread
.125" drill (Round engraving bit cutter head)

*Bearing spacers can be 3D printed, but brass tubing is better. Brass tubing with 5mm ID and 1.5mm walls is readily available.

## Assembly

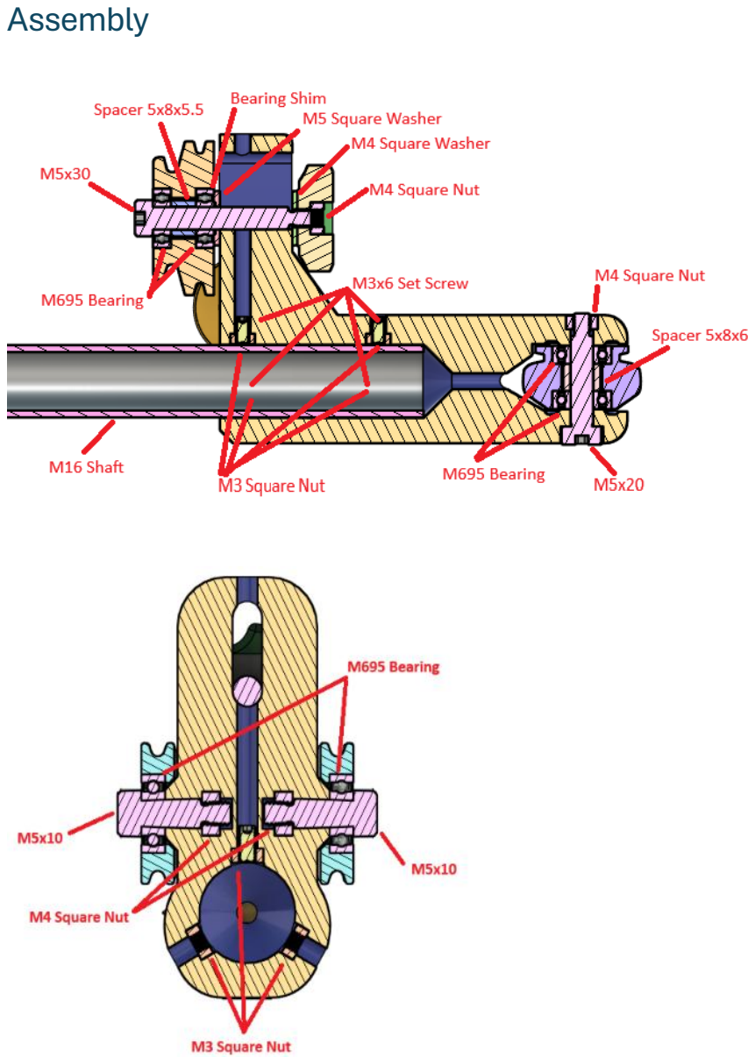
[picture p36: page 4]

## Shaft

- Insert M3 square nuts into the shaft opening. Note: Medium CA glue the inner three nuts to a short rod and use a long M3 screw to pull the nuts into their holes.
- Insert the 16mm diameter shaft and secure with six M3 set screws.
- Note: Shaft must be installed before the pulleys.

## Idler Pulleys

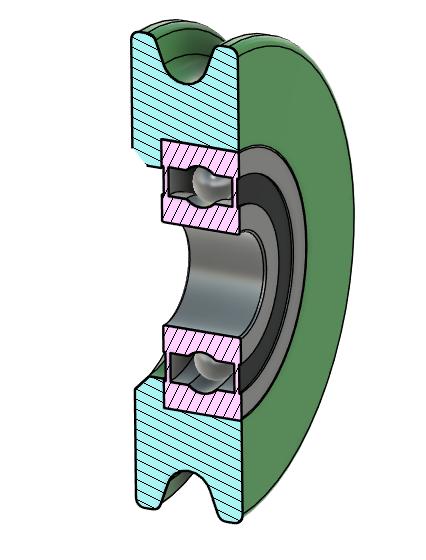
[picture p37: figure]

- Press the M695ZZ bearings into the idler pulleys.

- Press M4 square nuts into the openings at the back of the main arm.
- Attach the idler pulleys to the main arm using M5x10 shoulder bolts. Note: Metric shoulder bolts come with different thread sizes, so ensure yours have M4 threads.

## Drive pulley

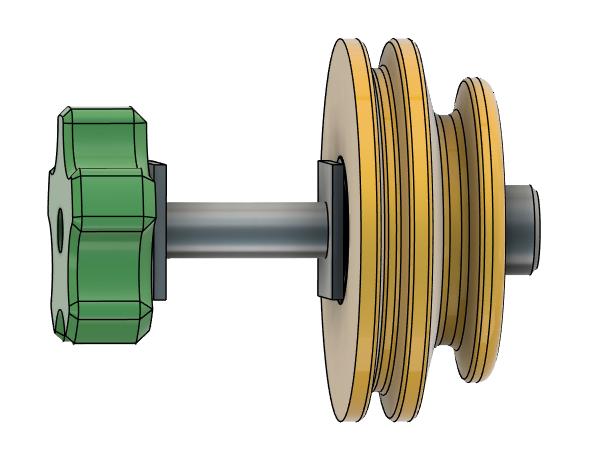
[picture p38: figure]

- Install the M695ZZ bearings and double pulley bearing spacer into the double pulley.
- Press the M4 heat set insert into the knob.
- Install the pulley using an M5x25 shoulder bolt, bearing shim, and washer. Use a washer and the knob to secure it. Note: The larger diameter pulley is next to the main arm.

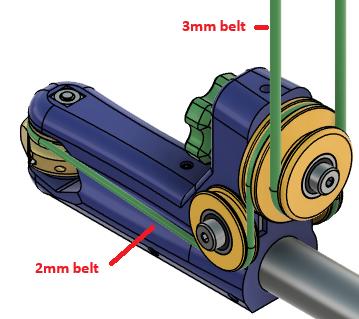
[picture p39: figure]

## Cutter heads

Three cutter head styles are included. The 1/8” engraving bit head is the simplest to assemble. The plain insert head requires careful tapping the M2.2 hole, while the brass nut insert head requires manufacturing the nut out of brass stock. Each style of the insert cutter heads come in clockwise (CW) and counterclockwise (CCW) versions.
Common assembly steps for all cutter heads:
- Press one M695 bearing into the head.
- Add the cutter head spacer 5mm X 8mm X 6mm.
- Press the second bearing into the head.
- Slide the cutter head into position and secure with the M5x20 shoulder bolt and M4 square nut.

## Insert head (Plain)

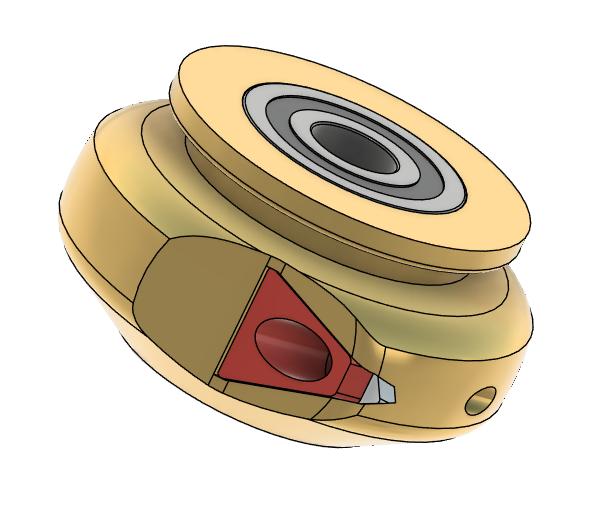
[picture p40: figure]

CW cutter head is shown

- Carefully tap the insert hole with 2.2mm tap.
- Attach the insert. It will be a tight fit. Do not over tighten the locking screw.
- Optional: Insert Top Lock can be installed using acetone to secure it. Using this may limit use to only one tip. Reprint the cutter head body to use the other tips.

## Insert head (Brass Nut)

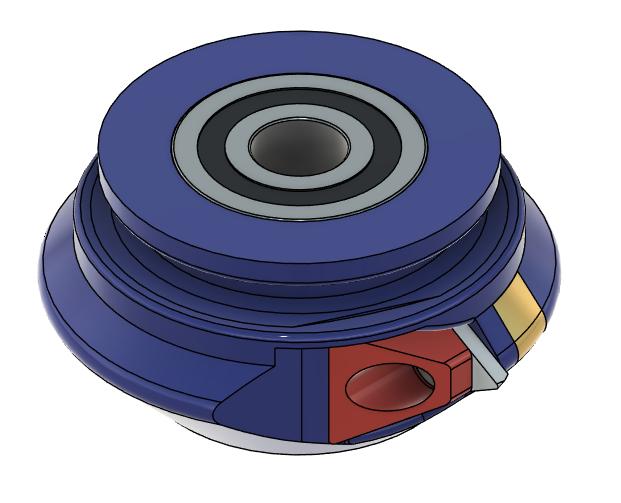
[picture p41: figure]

## Insert Nut

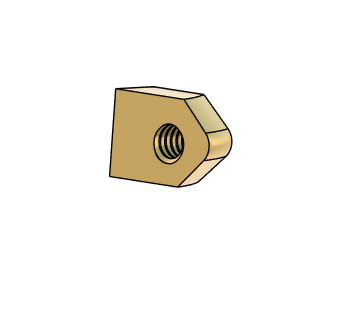
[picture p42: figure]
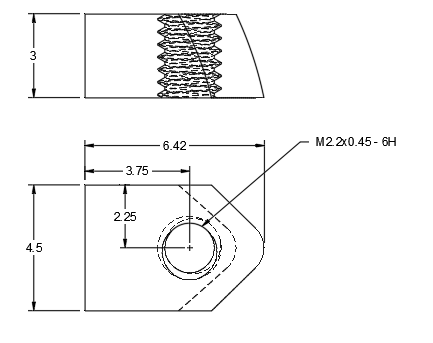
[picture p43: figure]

- Insert nut is the same for both CW and CCW versions.
- Drill and tap brass nut. Insert into opening. Final profile can be done quickly with a file.
- Attach insert with M2.2x6 torx screw.
- Optional: Insert Top Lock can be installed using acetone to secure it. Using this may limit use to only one tip. Other cutter heads can be printed to use the other tips.

## 1/8” engraving bit head

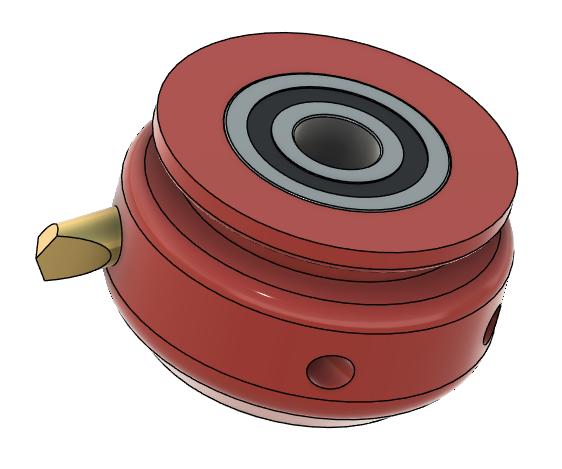
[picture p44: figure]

- Tap the locking screw holes with M3 tap.
- Install the engraving bit. The hole may need to be reamed or drilled first. The bit may be set for either CW or CCW rotation.
- Install the locking M3 set screws. Do not over tighten.

## Belts

- Belts must be cut to length and welded.
- Attach the 2mm round poly belt around the drive pulley, under the idler pulleys and around the cutter head.
- Belt tension is adjusted by moving the drive pulley up or down, then locked in place with the knob.
- The 3mm round poly belt runs between the drive pulley and the overhead drive. CCW rotation is achieved by twisting the belt 180 degrees.

## Engraving bit sharpening jigs

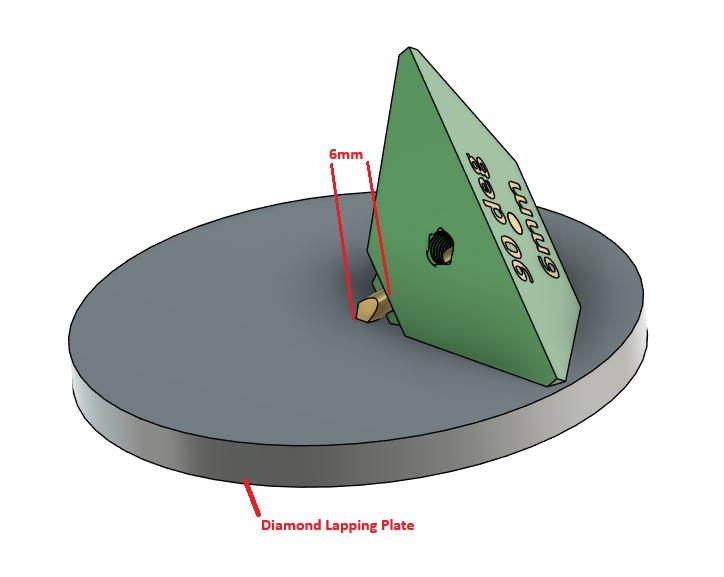
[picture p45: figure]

Jigs for 60, 90, and 120 degrees included angles are included. Secure the engraving bit in the jig using an M5x6mm set screw. Use diamond lapping plates to create the profiles on three sides. It is recommended to use at least 3000 grit for the final polishing. Even finer grits may give even better cut surfaces. Set the distance between the cutter tip and the ledge on the jig to the distance printed on the bottom of the jig, either 6mm or 10mm.

## 3D printer slicer settings

- Walls: 8.
- Infill: 40% Cubic.
- Brim: 12mm (Depends on how well your build plate works for small parts).
- Filament: ABS-GF for the main body and pulleys. ABS for the cutterheads and sharpening jigs.

## Main Body and pulleys

- .20 layer height

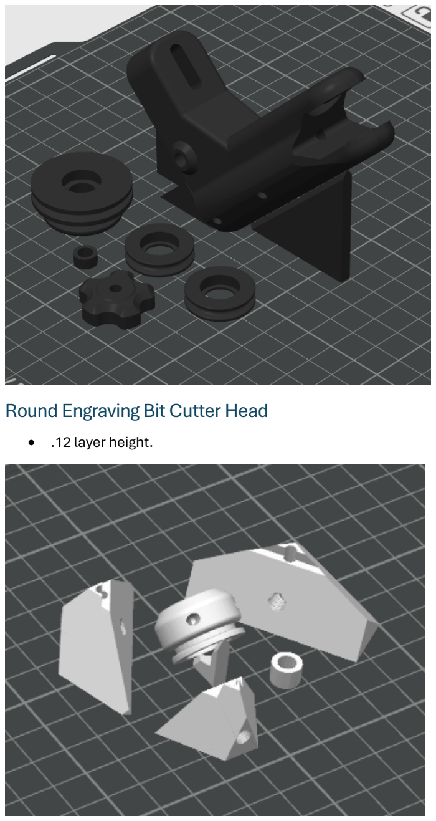
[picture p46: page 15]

## Round Engraving Bit Cutter Head

- .12 layer height.

## Triangular Insert Cutter Head Plain

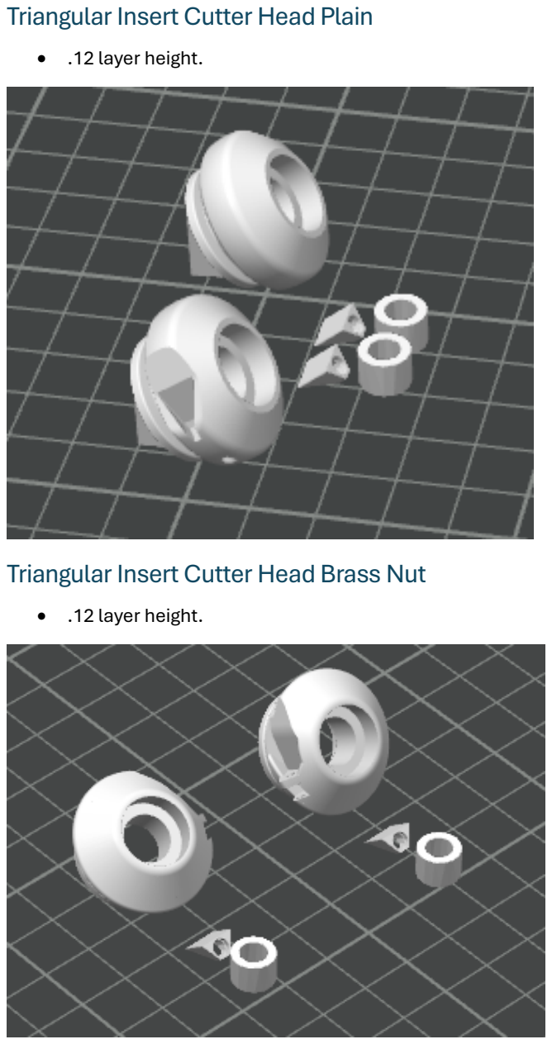
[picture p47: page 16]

- .12 layer height.

## Triangular Insert Cutter Head Brass Nut

- .12 layer height.

## Notes:

The pulleys and cutterhead should move freely.
The bearings in the pulleys may get hot to the touch when first running. This seems to diminish over time.
Do not take heavy cuts.
Models for clockwise and counterclockwise insert cutterheads are included as well as a model for 1/8” bits.
Sharpening jigs for 60 degree and 120 degree engraving bits are included.

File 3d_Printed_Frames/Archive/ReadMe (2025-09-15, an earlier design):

Universal Cutting Frame

.3mf files contain all of the parts for 3D printing this. The cutterhead file contains two insert cutterheads, 1 engraving bit cutterhead, and 2 sharpening templates for engraving bits.
Fusion and step files are included to allow modeling changes or individual printing.
Excel file contains the parts list.

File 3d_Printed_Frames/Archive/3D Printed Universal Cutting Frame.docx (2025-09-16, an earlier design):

# 3D Printed Universal Cutting Frame

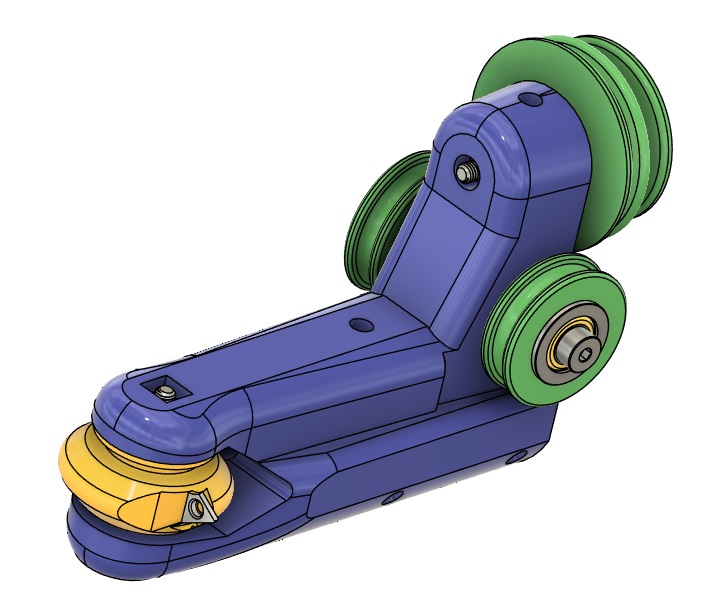
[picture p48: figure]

# Parts List

QTY | Description
2 | Shoulder bolt: M4x10(M3 thread 6mm long)
1 | Shoulder bolt: M4x20(M3 thread 6mm long)
1 | Shoulder bolt: M5x25(M4 thread 6mm long)
2 | M695ZZ bearing
6 | M104ZZ bearing
6 | M4 Bearing Shim: 4x7x0.2
5 | M4 Washer:4x9x0.8
1 | M5 Bearing Shim:5x7x0.2
1 | M5 Washer:5x10x1.1
9 | M3 square nut: 5.3x5.3x2.2
1 | M4 nut
6 | M3x6 Set screw
1 | Steel rod 16mmx120mm
1 | TDHB07T1202 Insert
1 | 1/8" Carbide rod: Minimum length 1"
1 | Round Poly belt: 2mm
| 3D printed parts
1 | Main body
1 | Cutter head: 1/8" (Brass or steel optional)
1 | Insert cutter head: CW
1 | Insert cutter head: CCW
2 | Idler pulleys
1 | Double pulley
1 | Double pulley spacer
1 | Sharpening jig: 1/8" 60 degrees
1 | Sharpening jig: 1/8" 120 degrees
| Tools
| Metric Allen wrenches: 1.5, 3
| Tap: 2.2mm

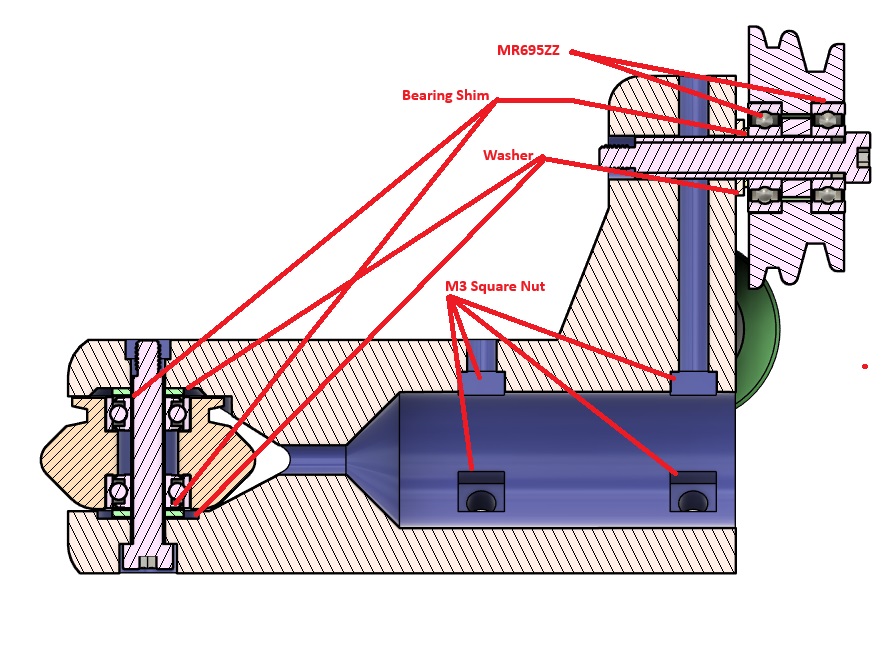
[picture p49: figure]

# Cutter heads

## Insert head

- Carefully tap the insert hole with 2.2mm tap. Don’t tap deeper than 4.5mm.
- Attach the insert. It will be a tight fit. Do not over tighten the locking screw.
- Press one MR104 bearing into the head.
- Add the cutterhead spacer.
- Press the second bearing into the head.
- Bearing shims and washers need to be held in place on the main arm. A drop of CA glue can help.
- Slide the cutterhead into position and secure with the M3x20 shoulder bolt and M3 square nut.

## 1/8” engraving bit head

- Tap the locking screw hole with M3 tap.
- Install the engraving bit. The hole may need to be reamed or drilled first.
- Install the locking M3 set screw. Do not over tighten.
- Install the bearings with the cutterhead spacer between them.
- Add the bearing shims and washers to the main arm.
- Install the cutterhead.

## Idler Pulleys

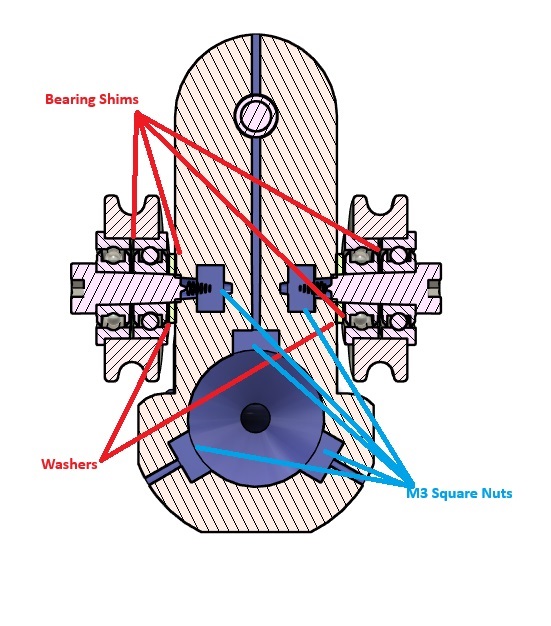
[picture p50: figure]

- Press the MR104ZZ bearings into the idler pulleys with two 0.2mm bearing shims between them.
- Press M3 square nuts into the openings at the back of the main arm.
- Attach the idler pulleys to the main arm using M4x10 shoulder bolts, bearing shims, and washers.

## Shaft

- Insert M3 square nuts into the shaft opening. Note: CA glue the inner three nuts to a short rod and use a long M3 screw to pull the nuts into their holes.
- Insert the 16mm diameter shaft and secure with six M3 set screws.

# Drive pulley

- Install the MR695ZZ bearings and double pulley spacer into the double pulley.
- Install the pulley using an M5x25 shoulder bolt, bearing shim, and washer. Use a washer and nut to secure it. Note: The larger diameter pulley is next to the main arm.
- Attach the 2mm round poly belt.

# 3D printer slicer settings

- Walls: 8
- Infill: 40% Cubic
- Brim: 15mm
- Filament: ABS-GF for the main body and pulleys. ABS for the cutterheads and sharpening jigs.

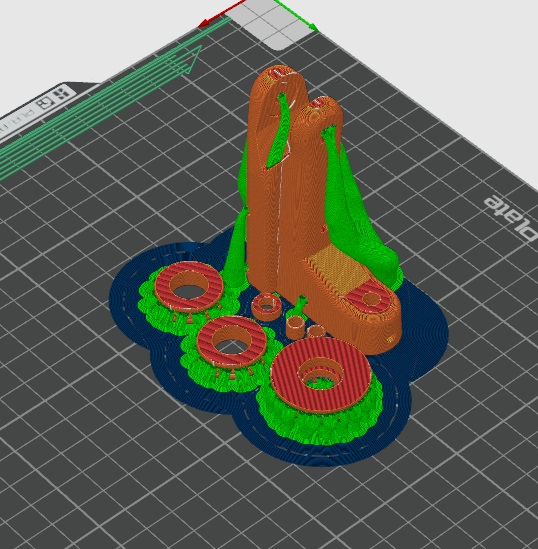
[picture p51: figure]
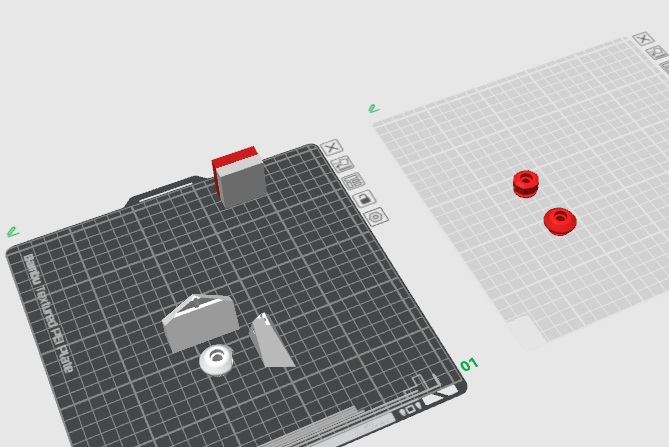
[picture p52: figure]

# Notes:

The pulleys and cutterhead should move freely.

The bearings in the pulleys may get hot to the touch when first running. This seems to diminish over time.

Do not take heavy cuts.

Models for clockwise and counterclockwise insert cutterheads are included as well as a model for 1/8” bits.

Sharpening jigs for 60 degree and 120 degree engraving bits are included.

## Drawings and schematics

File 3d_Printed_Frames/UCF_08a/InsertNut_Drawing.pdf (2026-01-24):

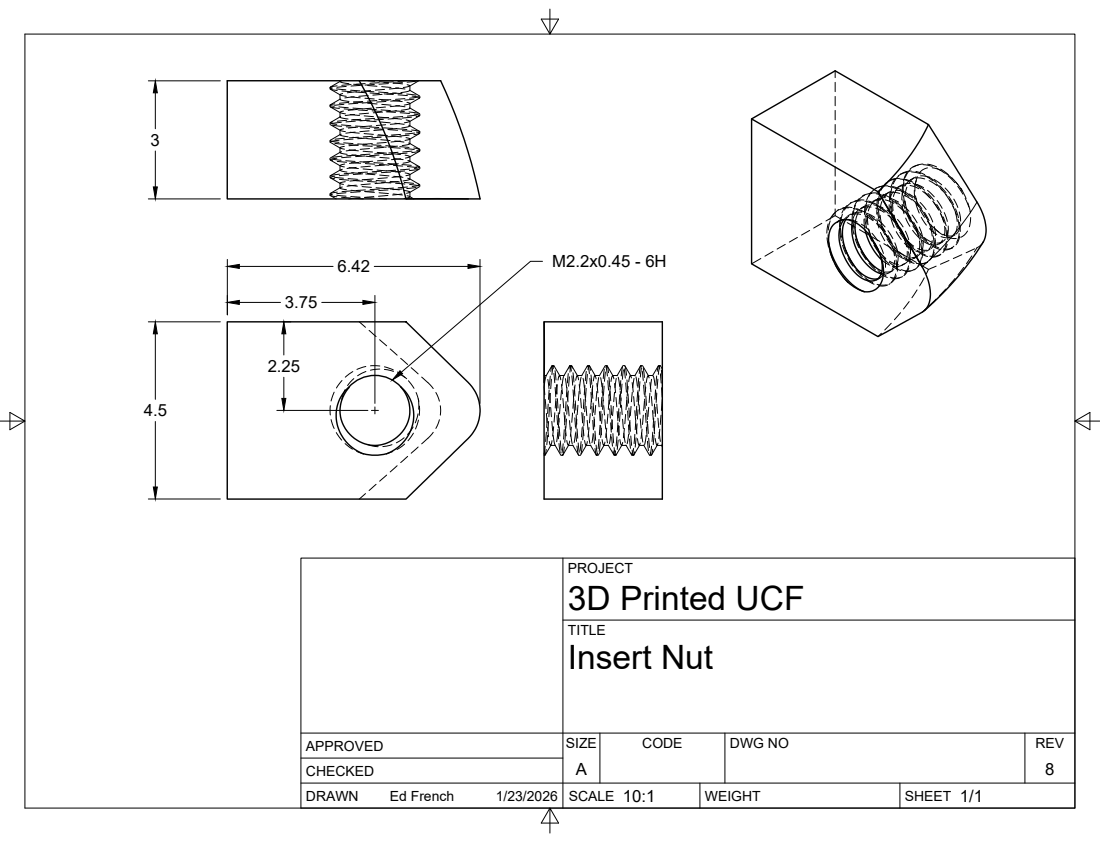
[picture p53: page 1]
SIZE; CODE; DWG NO; REV; Ed French; 3D Printed UCF; Insert Nut

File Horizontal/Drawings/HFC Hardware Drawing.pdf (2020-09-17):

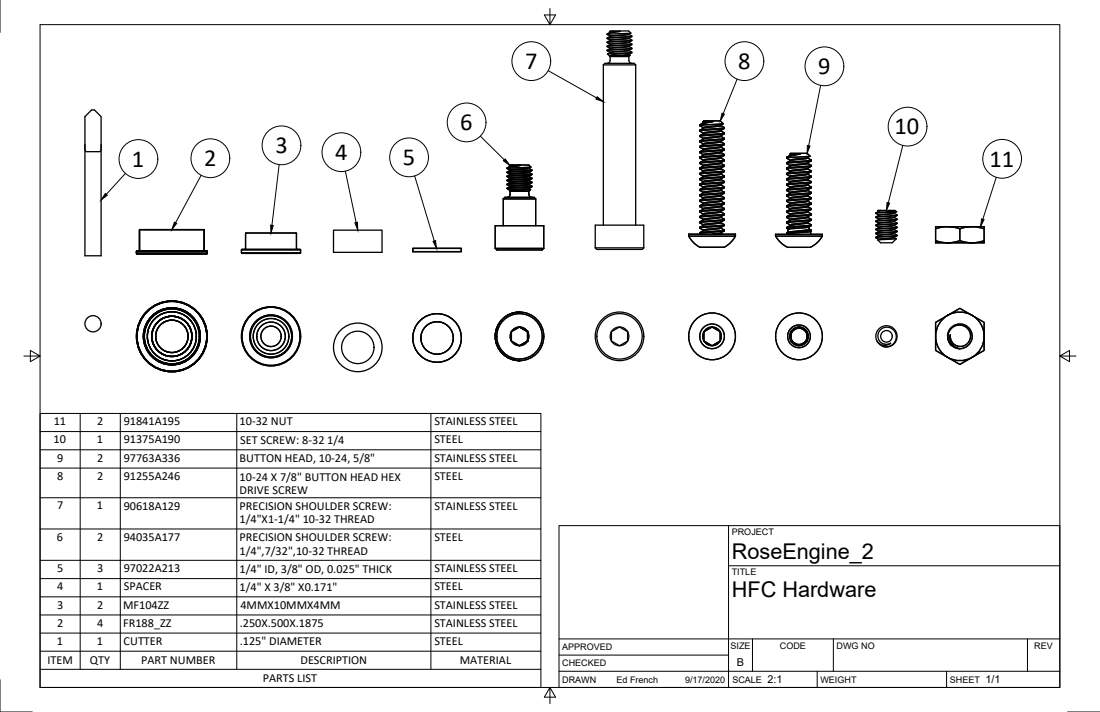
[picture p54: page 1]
SIZE; CODE; DWG NO; REV; Ed French; HFC Hardware; PARTS LIST

11 | 2 | 91841A195 | 10-32 NUT | STAINLESS STEEL
10 | 1 | 91375A190 | SET SCREW: 8-32 1/4 | STEEL
9 | 2 | 97763A336 | BUTTON HEAD, 10-24, 5/8" | STAINLESS STEEL
8 | 2 | 91255A246 | 10-24 X 7/8" BUTTON HEAD HEX DRIVE SCREW | STEEL

7 | 1 | 90618A129 | PRECISION SHOULDER SCREW: 1/4"X1-1/4" 10-32 THREAD | STAINLESS STEEL

6 | 2 | 94035A177 | PRECISION SHOULDER SCREW: 1/4",7/32",10-32 THREAD | STEEL

PROJECT RoseEngine_2

5 | 3 | 97022A213 | 1/4" ID, 3/8" OD, 0.025" THICK | STAINLESS STEEL
4 | 1 | SPACER | 1/4" X 3/8" X0.171" | STEEL
3 | 2 | MF104ZZ | 4MMX10MMX4MM | STAINLESS STEEL
2 | 4 | FR188_ZZ | .250X.500X.1875 | STAINLESS STEEL
1 | 1 | CUTTER | .125" DIAMETER | STEEL
ITEM | QTY | PART NUMBER | DESCRIPTION | MATERIAL

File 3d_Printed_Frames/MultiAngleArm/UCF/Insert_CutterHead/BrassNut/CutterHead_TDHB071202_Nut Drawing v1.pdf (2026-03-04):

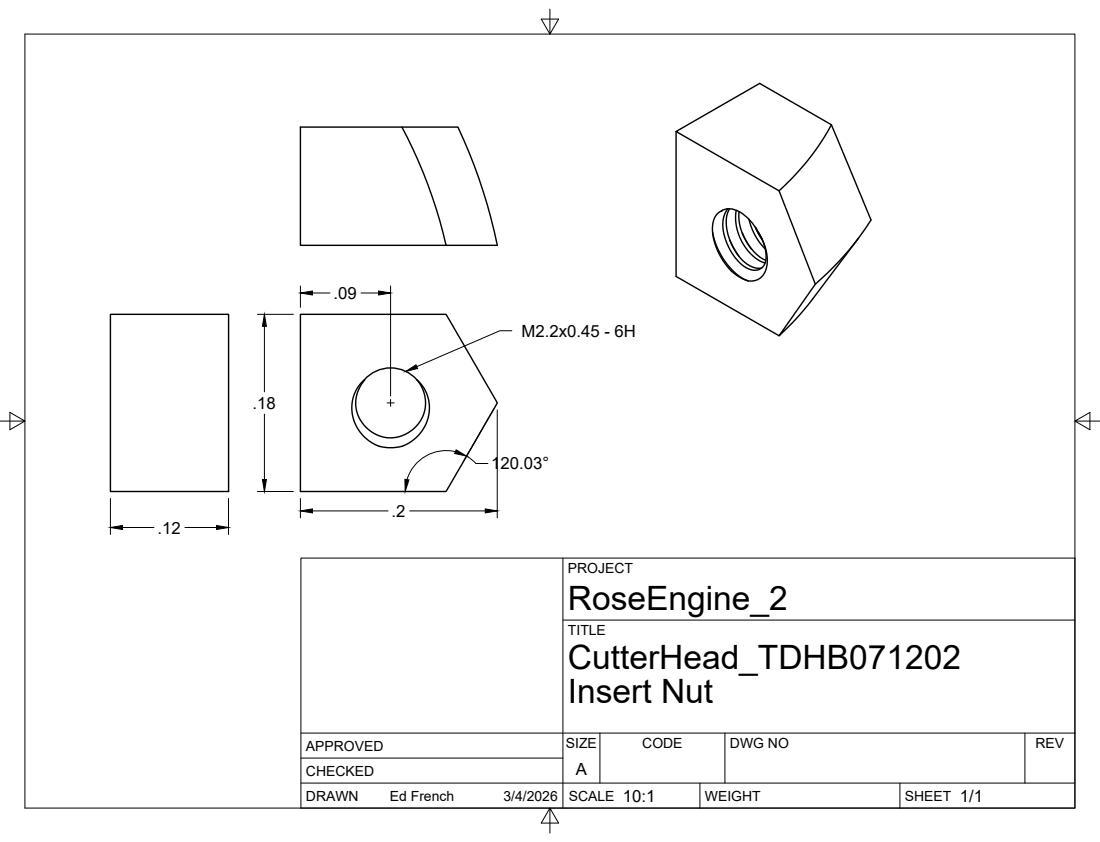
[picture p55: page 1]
SIZE; CODE; DWG NO; REV; Ed French; Insert Nut

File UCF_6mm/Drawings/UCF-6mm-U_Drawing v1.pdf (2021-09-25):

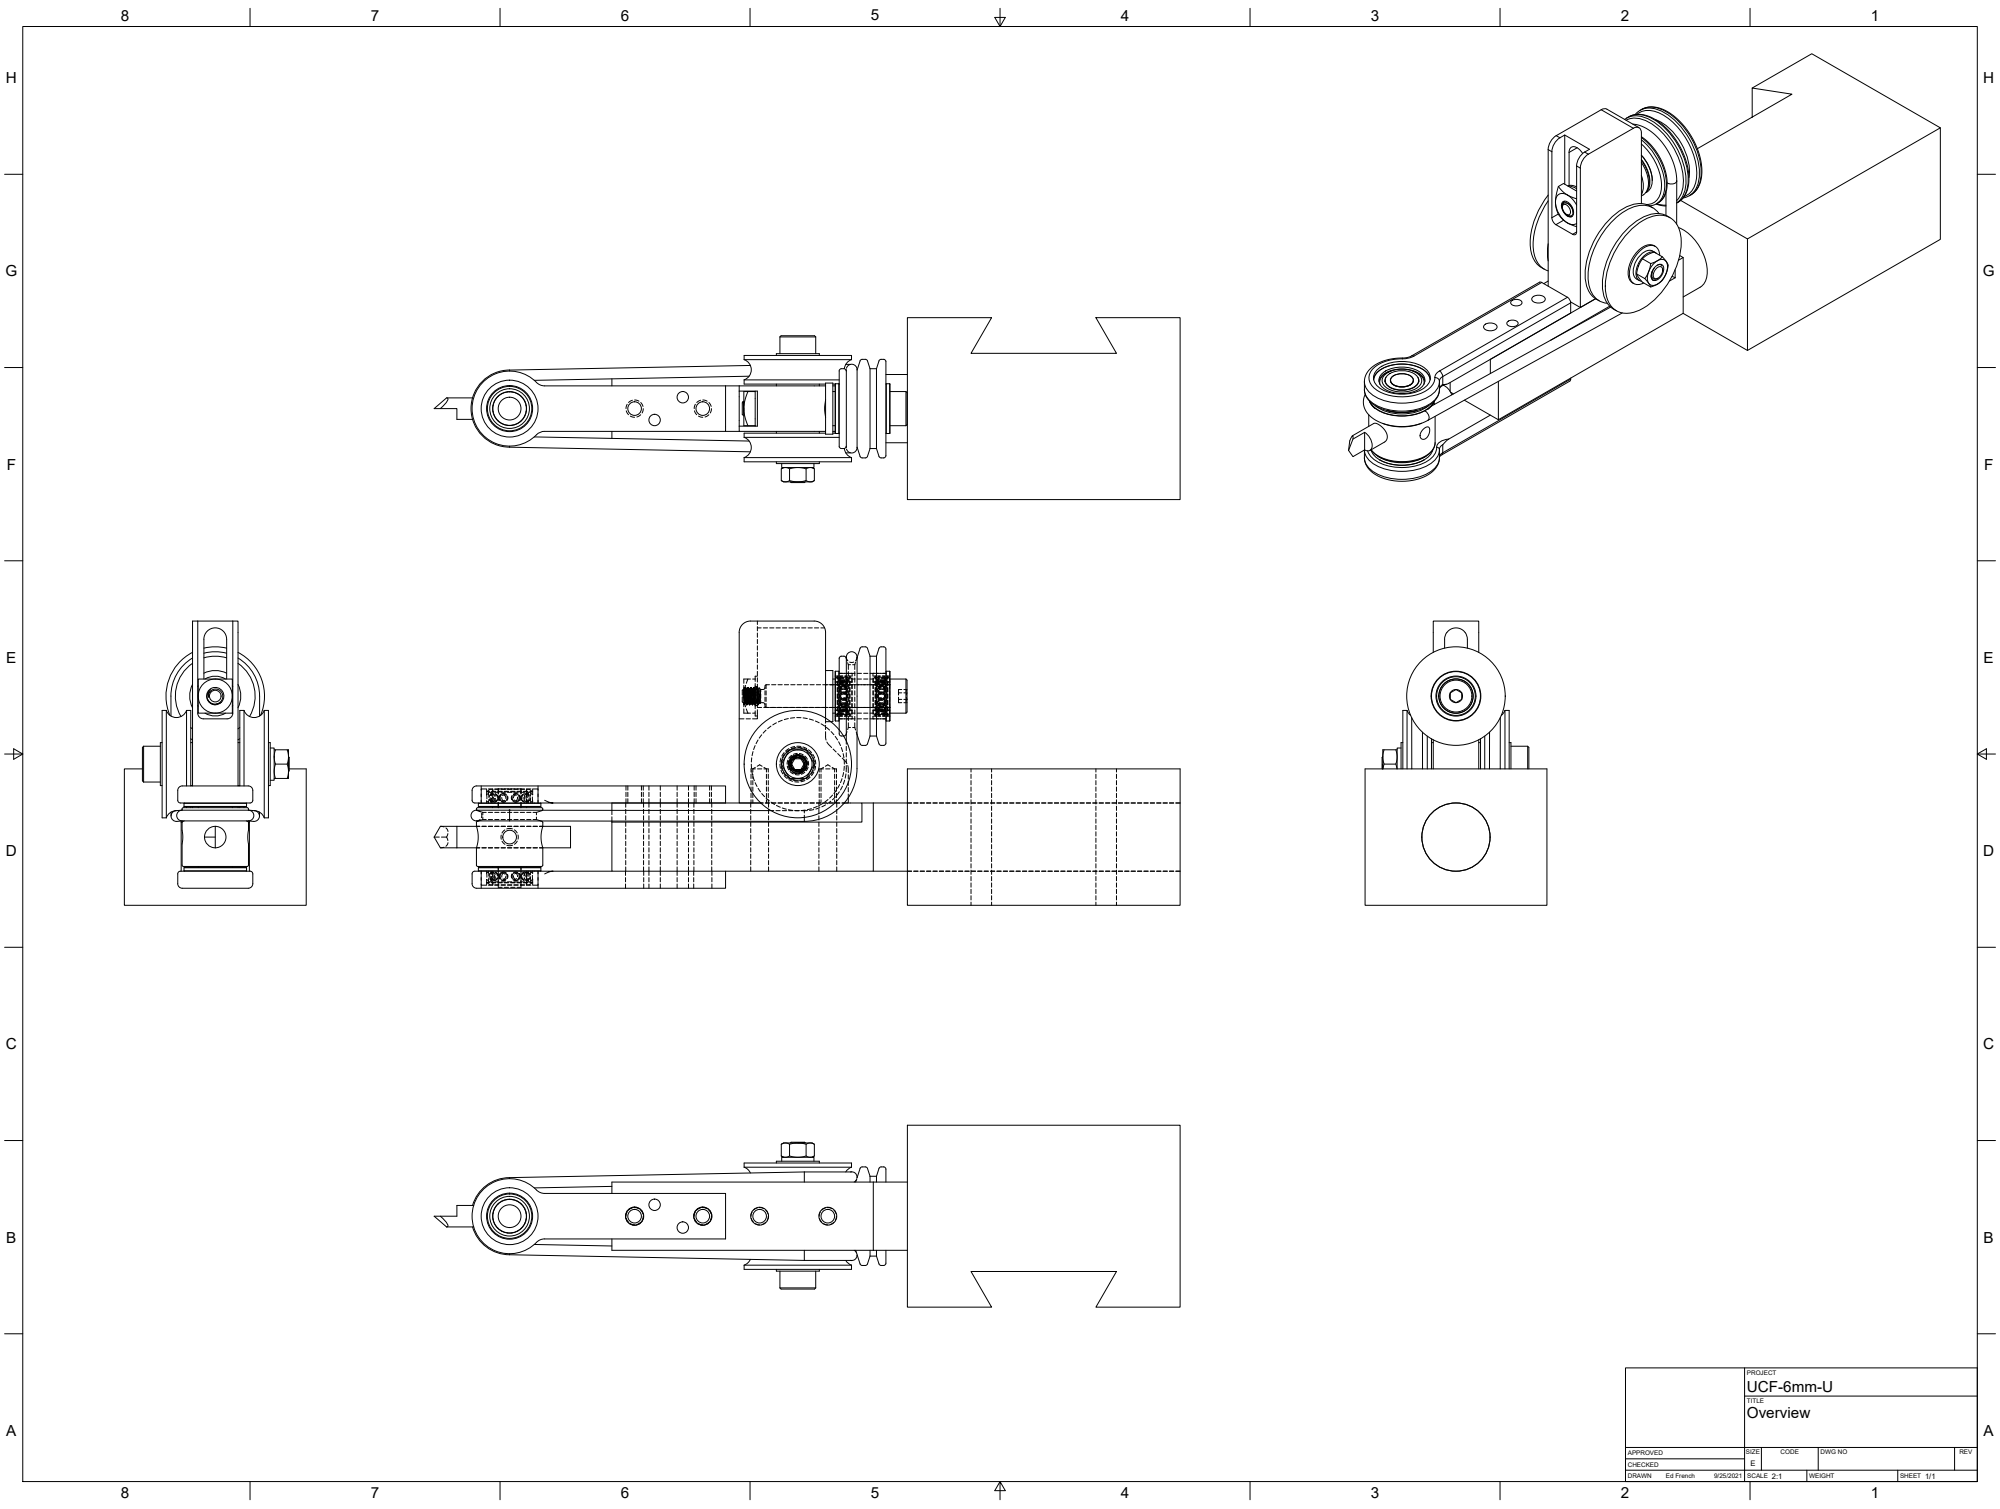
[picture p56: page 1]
PROJECT TITLE DRAWN CHECKED APPROVED; SCALE; WEIGHT; SHEET SIZE; CODE; DWG NO; REV Ed French; 1/1 EUCF-6mm-U Overview; BCDEFGH ABCDEFGH

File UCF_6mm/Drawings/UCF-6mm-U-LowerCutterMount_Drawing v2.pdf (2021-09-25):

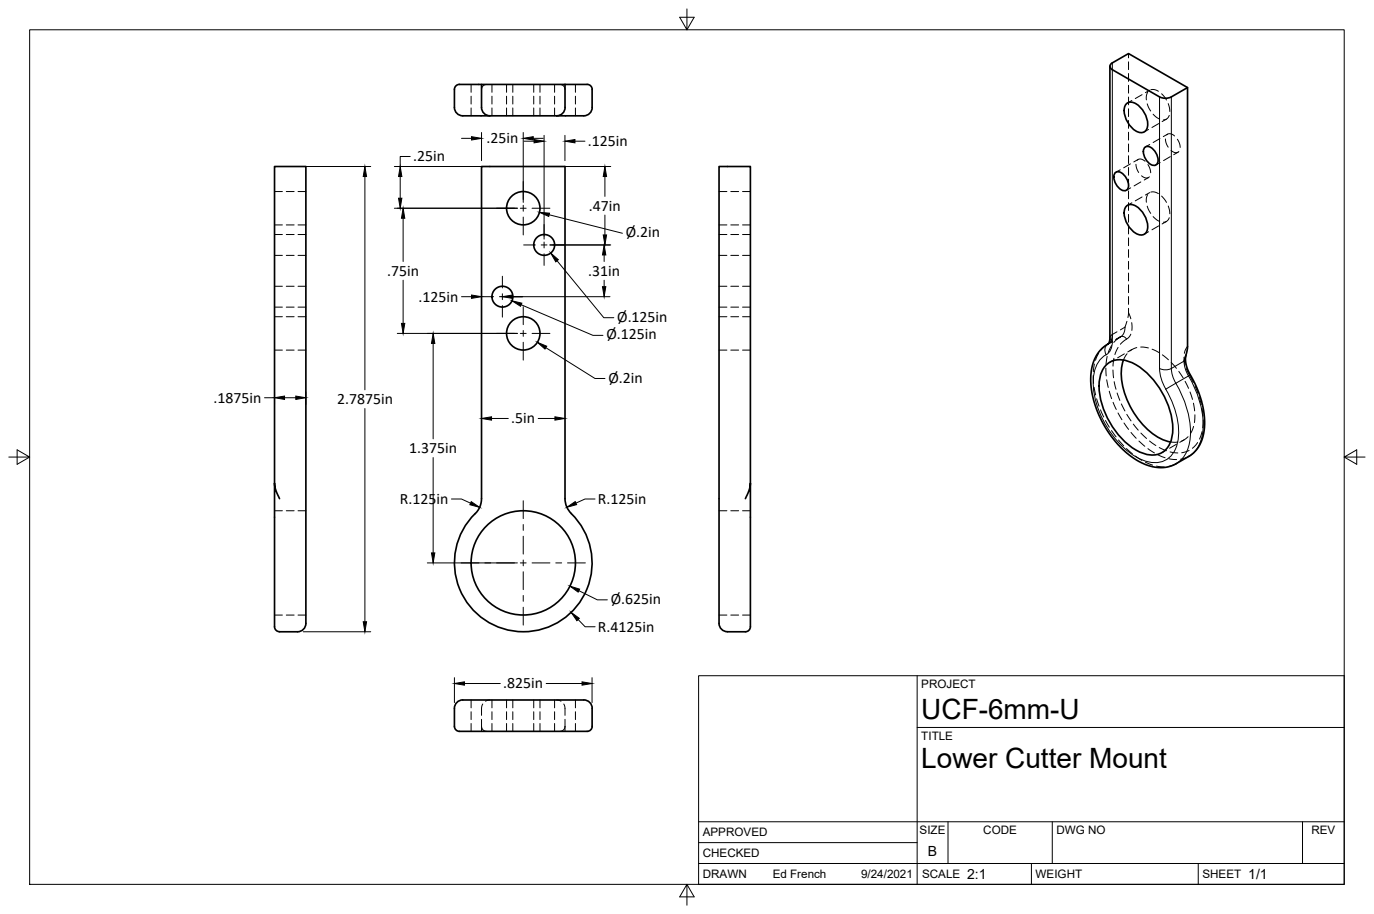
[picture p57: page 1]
SIZE; CODE; DWG NO; REV; Ed French

PROJECT
UCF-6mm-U
Lower Cutter Mount

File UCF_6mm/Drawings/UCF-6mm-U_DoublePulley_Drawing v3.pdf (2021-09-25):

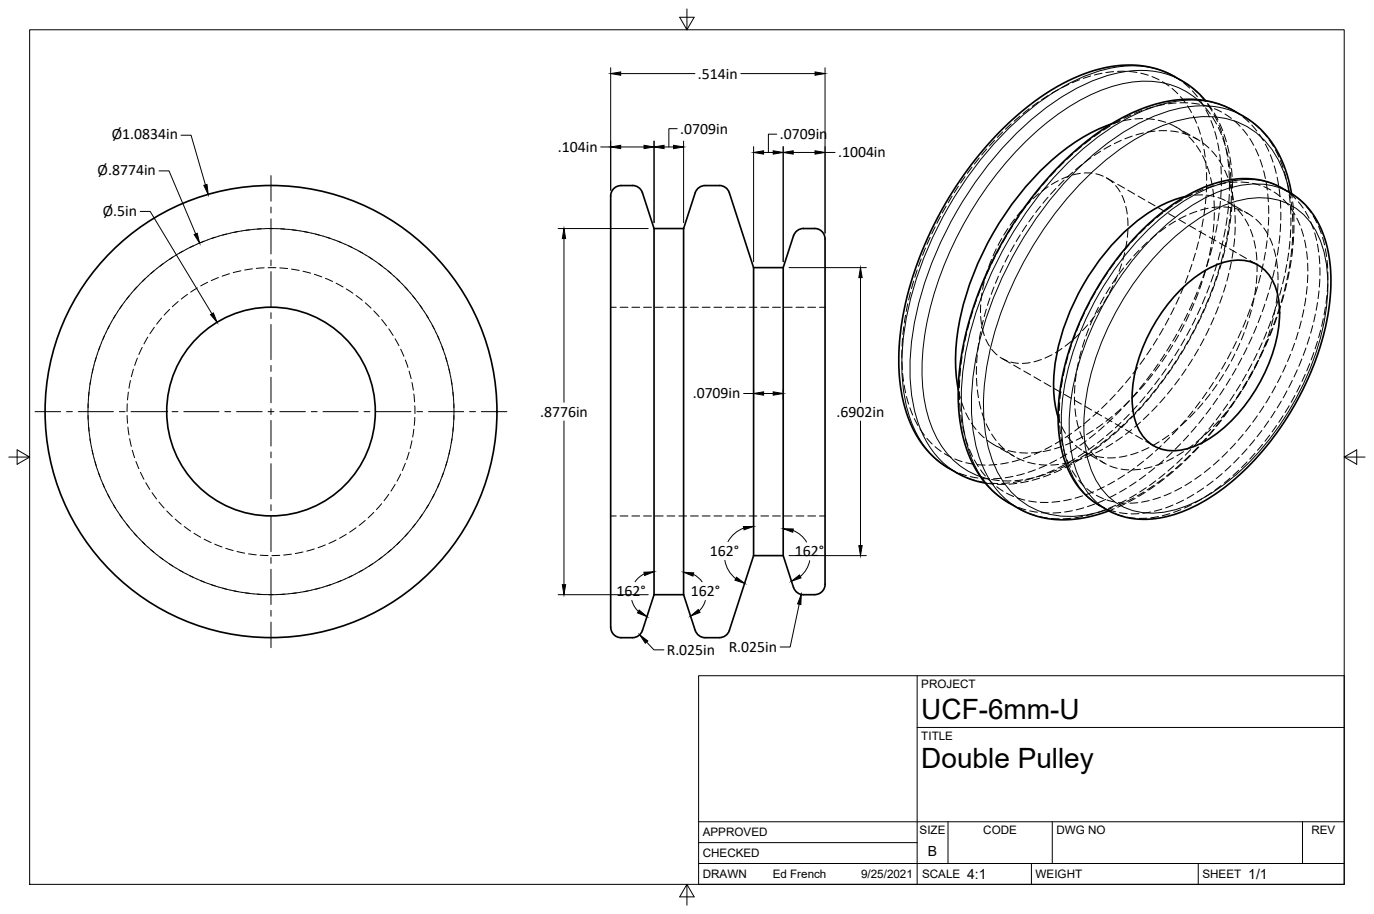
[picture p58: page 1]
SIZE; CODE; DWG NO; REV; Ed French; Double Pulley

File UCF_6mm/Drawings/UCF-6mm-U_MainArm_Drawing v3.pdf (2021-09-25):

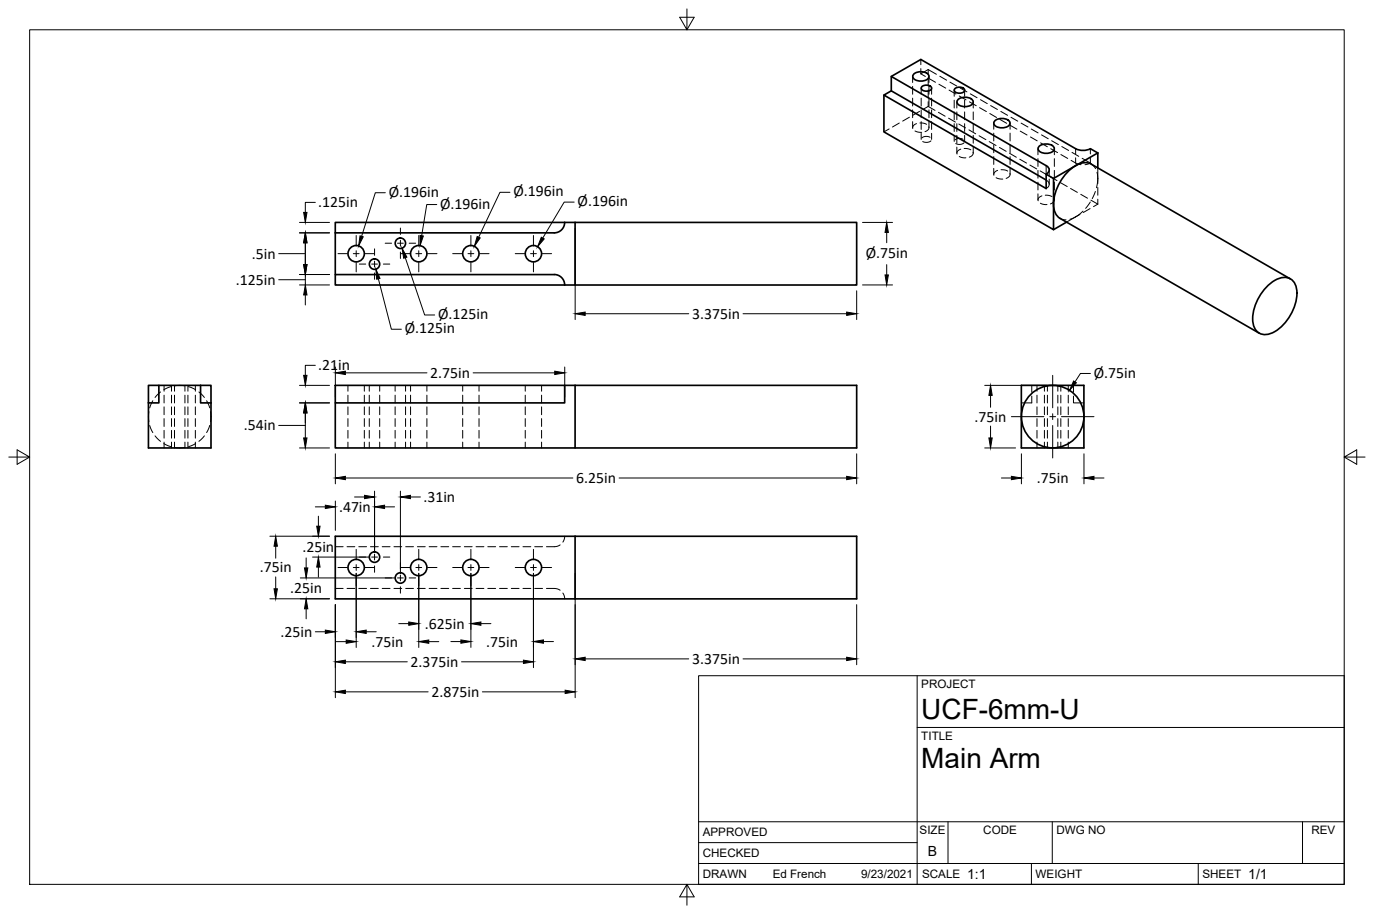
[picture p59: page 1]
SIZE; CODE; DWG NO; REV; Ed French; Main Arm

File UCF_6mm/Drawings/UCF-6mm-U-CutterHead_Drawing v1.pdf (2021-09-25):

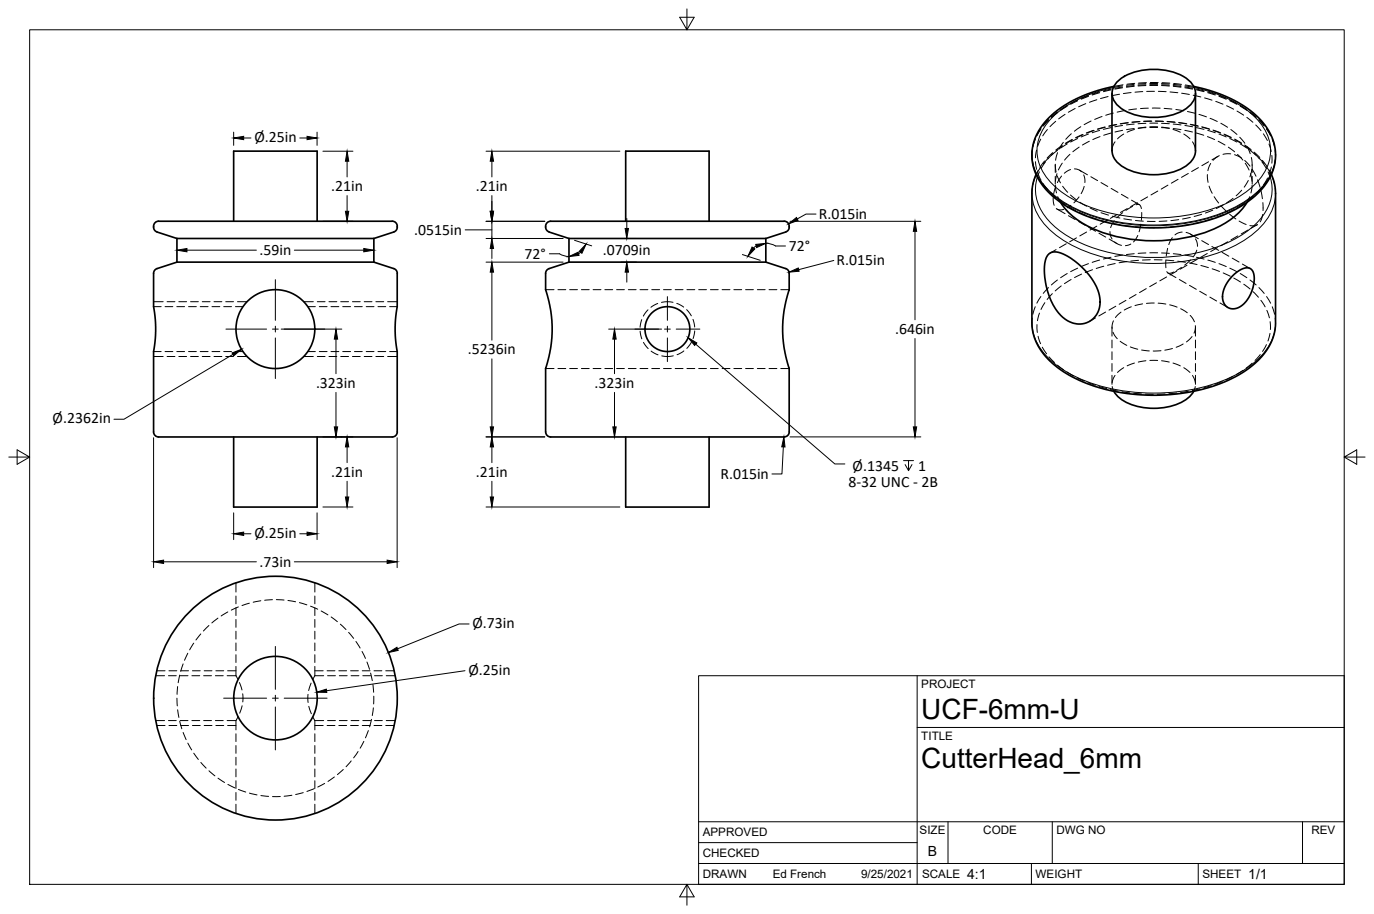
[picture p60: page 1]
SIZE; CODE; DWG NO; REV; Ed French; 8-32 UNC - 2B

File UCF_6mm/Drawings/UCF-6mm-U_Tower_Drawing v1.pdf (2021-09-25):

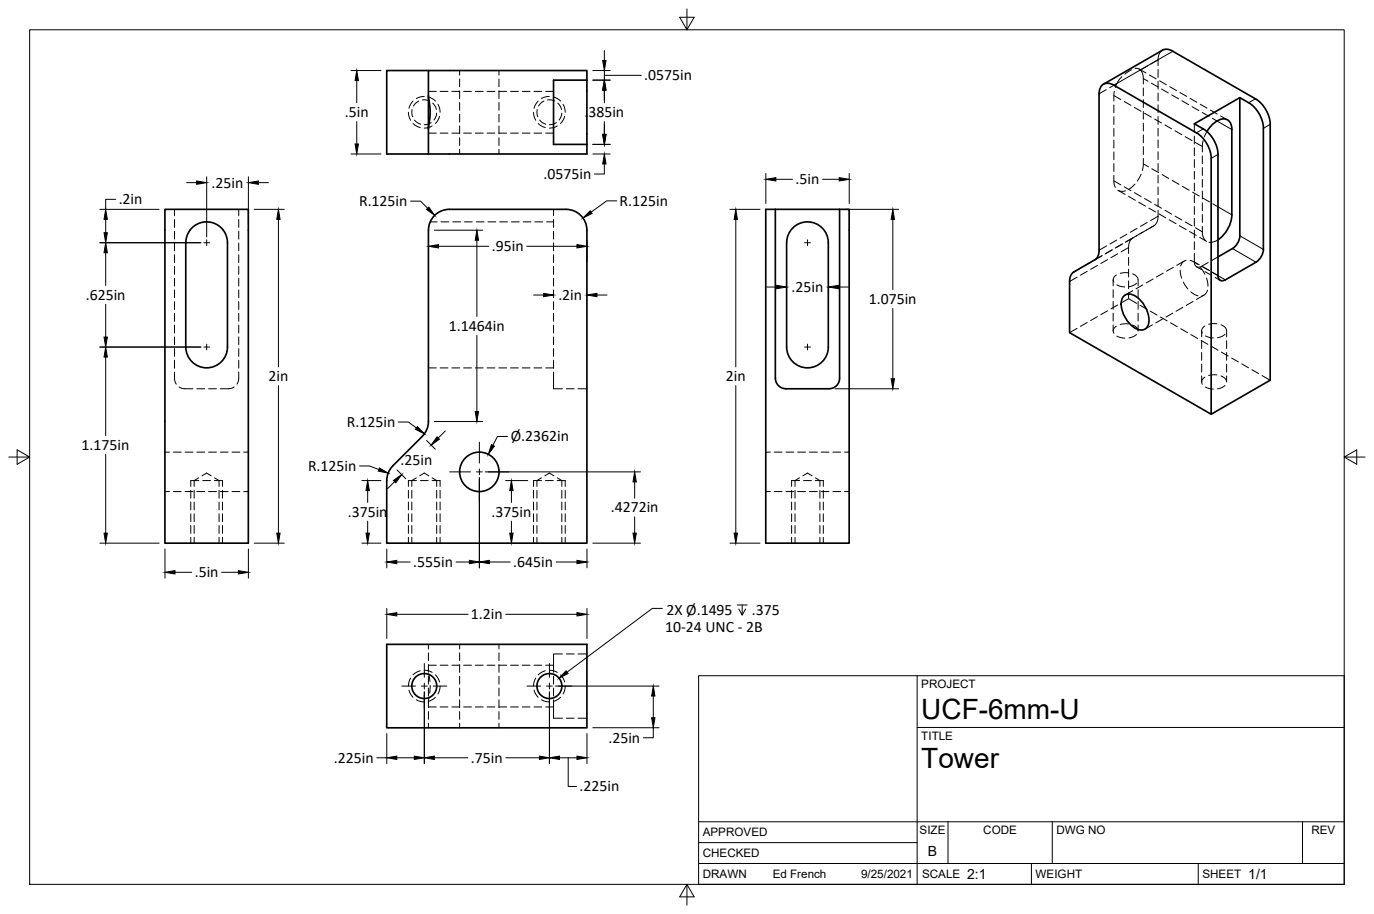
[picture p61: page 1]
SIZE; CODE; DWG NO; REV; Ed French; 10-24 UNC - 2B

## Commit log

2020-09-17 UCF-Sliding
    UCF with sliding pulley for belt tension adjustment
    [CutterHead_FR188ZZ.f3d, CutterHead_FR188ZZ_Alternate.f3z, DoublePulleyAssembly.f3d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]
2020-09-17 Remove
    Remove
    [CutterHead_FR188ZZ.f3d, CutterHead_FR188ZZ_Alternate.f3z, DoublePulleyAssembly.f3d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]
2020-09-17 UCF-Slotted
    Belt tension adjusted with pulley sliding in a slot.
    [90618A129 v2.f3d, 91251A248 v2.f3d, 91841A195 v3.f3d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]
2020-09-17 Horizontal Cutting Frame
    [90618A129.f3d, 91251A246.f3d, 91375A190.f3d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]
